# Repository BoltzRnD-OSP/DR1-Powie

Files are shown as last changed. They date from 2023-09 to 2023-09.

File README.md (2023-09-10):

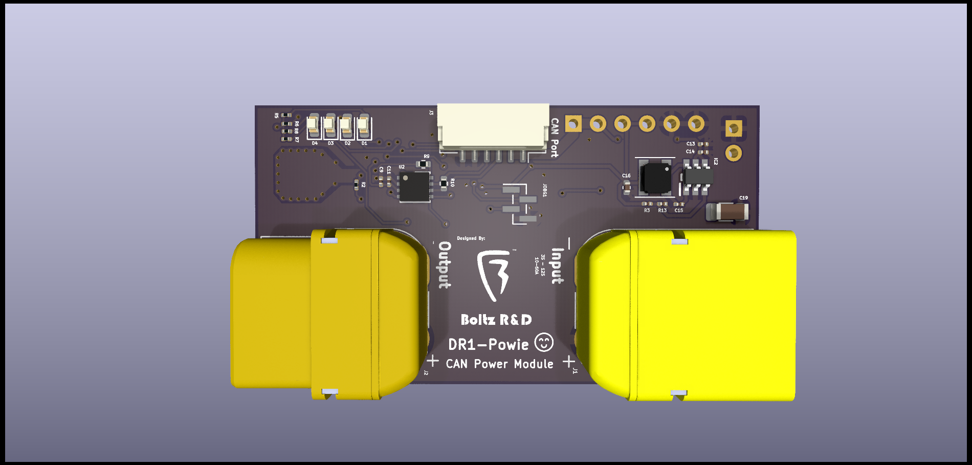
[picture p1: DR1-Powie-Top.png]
Board Top

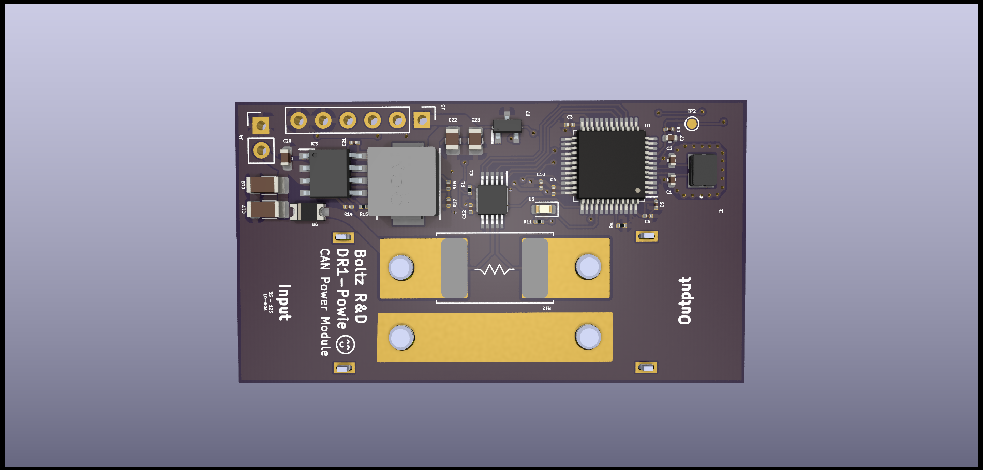
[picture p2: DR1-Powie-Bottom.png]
Board Bottom


# DR1-Powie ☺  
UAVCAN-Based Power Module for DR1 Series Flight Controllers

# Specifications:

Voltage: 3S - 12S  
Current Rating: 10A - 90A  
Embedded 5V 2A Buck to power the Flight Controller  
Battery Gauge LEDs (Will be functional in the near future)  

# License
This project is licensed under the Attribution-ShareAlike 4.0 International License.

You are free to commercially utilize the project and its derivatives. Please be generous and provide attribution! :)

THANKS!

Note: The Boltz R&D wordmark and lightning logo are trademarks of Boltz R&D. Any use other than for attribution of "this" project is strictly prohibited.

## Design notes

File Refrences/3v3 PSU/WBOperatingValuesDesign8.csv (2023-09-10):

Name | Value | Category | Description
Vout | 3.3 V | System Information | Operational Output Voltage
IC Tolerance | 20 mV | IC | IC Feedback Tolerance
Cin IRMS | 143.62 mA | Capacitor | Input capacitor RMS ripple current
Cin Pd | 83.7 µW | Capacitor | Input capacitor power dissipation
Cout IRMS | 59.6 mA | Capacitor | Output capacitor RMS ripple current
Cout Pd | 5.33 µW | Capacitor | Output capacitor power dissipation
Cinx IRMS | 8.96 mA | Capacitor | Bulk capacitor RMS ripple current
Cinx Pd | 1.61 µW | Capacitor | Bulk capacitor power dissipation
L Ipp | 206.46 mA | Inductor | Peak-to-peak inductor ripple current
L Pd | 11.23 mW | Inductor | Inductor power dissipation
Ipp percentage | 68.82% | Inductor | Inductor ripple current percentage (with respect to average inductor current)
Duty Cycle | 62.68% | System Information | Duty cycle
Efficiency | 93.5% | System Information | Steady state efficiency
Frequency | 1.1 MHz | System Information | Switching frequency
IC Tj | 34.56 °C | IC | IC junction temperature
IC Pd | 56.96 mW | IC | IC power dissipation
Pout | 990 mW | System Information | Total output power
Iin Avg | 192.44 mA | IC | Average input current
IC Ipk | 403.23 mA | IC | Peak switch current in IC
Mode | CCM | System Information | Conduction Mode
Vout p-p | 1.59 mV | System Information | Peak-to-peak output ripple voltage
Vin p-p | 39.07 mV | System Information | Peak-to-peak input voltage
Phase Marg | 62.56 ° | System Information | Bode Plot Phase Margin
Cross Freq | 25.32 kHz | System Information | Bode plot crossover frequency
Low Freq Gain | 63.92 dB | System Information | Gain at 1Hz
Gain Marg | -20.31 dB | System Information | Bode Plot Gain Margin
ICThetaJA Effective | 80 °C/W | IC | Effective IC Junction-to-Ambient Thermal Resistance
FootPrint | 77 mm² | System Information | Total Foot Print Area of BOM components
Vout Actual | 3.33 V | System Information | Vout Actual calculated based on selected voltage divider resistors
Vout Tolerance | 4.07% | System Information | Vout Tolerance based on IC Tolerance (no load) and voltage divider resistors if applicable
Vin | 5.5 V | System Information | Vin operating point
Iout | 300 mA | System Information | Iout operating point
Cin Pd | 83.7 µW | Power | Input capacitor power dissipation
Cout Pd | 5.33 µW | Power | Output capacitor power dissipation
Cinx Pd | 1.61 µW | Power | Bulk capacitor power dissipation
L Pd | 11.23 mW | Power | Inductor power dissipation
IC Pd | 56.96 mW | Power | IC power dissipation
Total BOM | $0.44 | System Information | Total BOM Cost
Total Pd | 68.4 mW | Power | Total Power Dissipation
BOM Count | 9 | System Information | Total Design BOM count

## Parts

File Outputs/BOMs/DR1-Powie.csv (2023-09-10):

Id | Designator | Footprint | Quantity | Designation | Supplier and ref
1 | C24 | C_0402_1005Metric | 1 | 100nf 100V | GRM155R62A104KE14D
2 | IC1 | SOP50P490X110-10N | 1 | INA239AIDGSR | INA239AIDGSR
3 | R12 | BVS-M-R0005-1.0 | 1 | 0.5MOhm 9W | BVS-M-R0005-1.0
4 | R19,R18 | R_0201_0603Metric | 2 | 220E 0.1% | ERA-1AEB221C
5 | D6 | D_MicroSMP_AK | 1 | V2PM10HM3/H | V2PM10HM3/H
6 | C2,C1 | C_0402_1005Metric | 2 | 8pF 1% | GCM1555C1H8R0FA16D
7 | C18,C17,C19 | C_1206_3216Metric | 3 | 4.7uF 63V | GRM31CC72A475ME11L
8 | C10,C13 | C_0201_0603Metric | 2 | 4.7uF | GRM035R60J475ME15D
9 | R14 | C_0201_0603Metric | 1 | 64.9K | RC0201FR-0764K9L
10 | IC3 | SOIC127P600X170-9N | 1 | LMR38020SDDAR | LMR38020SDDAR
11 | J5 | PinHeader_1x06_P2.54mm_Vertical | 1 | Conn_01x06 | ~
12 | TP2 | TestPoint_Pad_D1.0mm | 1 | TestPoint | ~
13 | R11,R6,R5,R7,R8 | R_0201_0603Metric | 5 | 220E | ERJ-1GNJ221C
14 | C23,C22 | C_0805_2012Metric | 2 | 47uF | GRM21BR60J476ME01K
15 | C6,C12,C3,C21,C4,C5,C14,C15 | C_0201_0603Metric | 8 | 100nf | CL03A104KQ3NNNC
16 | J4 | PinHeader_1x02_P2.54mm_Vertical | 1 | Conn_01x02 | ~
17 | R17 | C_0201_0603Metric | 1 | 10K 1% | ERJ-1GNF1002C
18 | C7 | C_0402_1005Metric | 1 | 10nf | C0402C103K4REC7411
19 | C20 | C_0603_1608Metric | 1 | 100nf 100V | CL10B104KC8NNNC
20 | R15 | R_0201_0603Metric | 1 | 100K | RC0201FR-07100KL
21 | D5,D2,D1,D4,D3 | LED_0603_1608Metric | 5 | LED | B1911USD-20D000114U1930
22 | L2 | INDPM7265X400N | 1 | 15uH 2A(Min) | SRP6540-150M
23 | R1,R4,R2 | R_0201_0603Metric | 3 | 10K | ERJ-1GNF1002C
24 | Y1 | NX3225GD8MHZSTDCRA3 | 1 | NX3225GD-8MHZ-EXS00A-CG04874 | NX3225GD-8MHZ-EXS00A-CG04874
25 | C8 | C_0201_0603Metric | 1 | 1uF | CL03A105MQ3CSNH
26 | R16 | C_0201_0603Metric | 1 | 40.2K 1% | RMCF0201FT40K2
27 | D7 | SOT95P230X117-3N | 1 | CDSOT23-T24CAN | CDSOT23-T24CAN
28 | U1 | LQFP-48_7x7mm_P0.5mm | 1 | STM32L431CBTx | STM32L431CBT6
29 | JDBG1 | PinHeader_1x04_P1.00mm_Vertical_SMD_Pin1Left | 1 | Conn_01x04 | ~
30 | C11,C9 | C_0201_0603Metric | 2 | 100nF | CL03A104KQ3NNNC
31 | R9 | R_0402_1005Metric | 1 | 10K | ERJ-1GNF1002C
32 | C16 | C_0402_1005Metric | 1 | 10uF | GRM155R60J106ME05J
33 | J2 | AMASS_XT60PW-F_1x02_P7.20mm_Horizontal | 1 | Conn_01x02 | AMASS_XT60PW-F
34 | U2 | DFN-8-1EP_3x3mm_P0.65mm_EP1.55x2.4mm | 1 | TJA1051TK-3 | TJA1051TK-3
35 | J1 | AMASS_XT60PW-M_1x02_P7.20mm_Horizontal | 1 | Conn_01x02 | AMASS_XT60PW-M
36 | R3 | C_0201_0603Metric | 1 | 69.8K | ERJ-1GNF6982C
37 | L1 | Inductor | 1 | 5.6uH 0.6A(Min) | 78438356056
38 | J3 | JST_GH_SM06B-GHS-TB_1x06-1MP_P1.25mm_Horizontal | 1 | Conn_01x06 | JST_GH_SM06B-GHS-TB
39 | R13 | C_0201_0603Metric | 1 | 22.1K | ERJ-1GNF2212C
40 | IC2 | SOT95P280X145-6N | 1 | LMR54406DBVR | LMR54406DBVR
41 | R10 | R_0402_1005Metric | 1 | 120E | CRCW0402120RJNED

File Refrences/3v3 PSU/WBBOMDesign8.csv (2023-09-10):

Part | Manufacturer | Part Number | Quantity | Price ($) | Footprint (mm²) | Description
Rfbb | Vishay-Dale | CRCW040222K1FKED | 1 | 0.01 | 3 | Resistance: 22.1 kΩ Tolerance: 1.0% Power: 63 mW
Rfbt | Vishay-Dale | CRCW040269K8FKED | 1 | 0.01 | 3 | Resistance: 69.8 kΩ Tolerance: 1.0% Power: 63 mW
Cinx | MuRata | GRM188R71H104KA93D | 1 | 0.02 | 4.68 | Cap: 100 nF Total Derated Cap: 100 nF VDC: 50 V ESR: 20 mΩ Package: 0603
L1 | NIC Components | NPI43C5R6MTRF | 1 | 0.07 | 30.74 | L: 5.6 µH DCR: 120 mΩ IDC: 1.8 A
U1 | Texas Instruments | LMR54406DBVR | 1 | 0.227 | 14.82
Cboot | MuRata | GRM155R71C104KA88D | 1 | 0.01 | 3 | Cap: 100 nF Total Derated Cap: 100 nF VDC: 16 V ESR: 1 mΩ Package: 0402
Cin | TDK | C1608X7R1A225K080AC | 1 | 0.03 | 4.68 | Cap: 2.2 µF Total Derated Cap: 1.6 µF VDC: 10 V ESR: 4.06 mΩ Package: 0603
Cout | Kemet | C0805C106K8PACTU | 2 | 0.03 | 6.75 | Cap: 10 µF Total Derated Cap: 15 µF VDC: 10 V ESR: 3 mΩ Package: 0805

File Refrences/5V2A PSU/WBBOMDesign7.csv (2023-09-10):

Part | Manufacturer | Part Number | Quantity | Price ($) | Footprint (mm²) | Description
Rfbt | Vishay-Dale | CRCW040240K2FKED | 1 | 0.01 | 3 | Resistance: 40.2 kΩ Tolerance: 1.0% Power: 63 mW
Rfbb | Vishay-Dale | CRCW040210K0FKED | 1 | 0.01 | 3 | Resistance: 10 kΩ Tolerance: 1.0% Power: 63 mW
Rpgood | Vishay-Dale | CRCW0603100KFKEA | 1 | 0.01 | 4.68 | Resistance: 100 kΩ Tolerance: 1.0% Power: 100 mW
Cboot | MuRata | GRM155R71C104KA88D | 1 | 0.01 | 3 | Cap: 100 nF Total Derated Cap: 100 nF VDC: 16 V ESR: 1 mΩ Package: 0402
Cinx | TDK | C2012X7R2A104K125AA | 1 | 0.03 | 6.75 | Cap: 100 nF Total Derated Cap: 100 nF VDC: 100 V ESR: 20.73 mΩ Package: 0805
Rt | Vishay-Dale | CRCW060364K9FKEA | 1 | 0.01 | 4.68 | Resistance: 64.9 kΩ Tolerance: 1.0% Power: 100 mW
L1 | NIC Components | NPI52W150MTRF | 1 | 0.264 | 358.11 | L: 15 µH DCR: 36 mΩ IDC: 4 A
Cout | MuRata | GRM32ER61C476KE15L | 2 | 0.17 | 14.7 | Cap: 47 µF Total Derated Cap: 63 µF VDC: 16 V ESR: 3.04 mΩ Package: 1210
Cin | TDK | C3225X7S2A475M200AB | 3 | 0.45 | 14.7 | Cap: 4.7 µF Total Derated Cap: 3.6 µF VDC: 100 V ESR: 5.89 mΩ Package: 1210
U1 | Texas Instruments | LMR38020FDDAR | 1 | 0.596 | 55.2

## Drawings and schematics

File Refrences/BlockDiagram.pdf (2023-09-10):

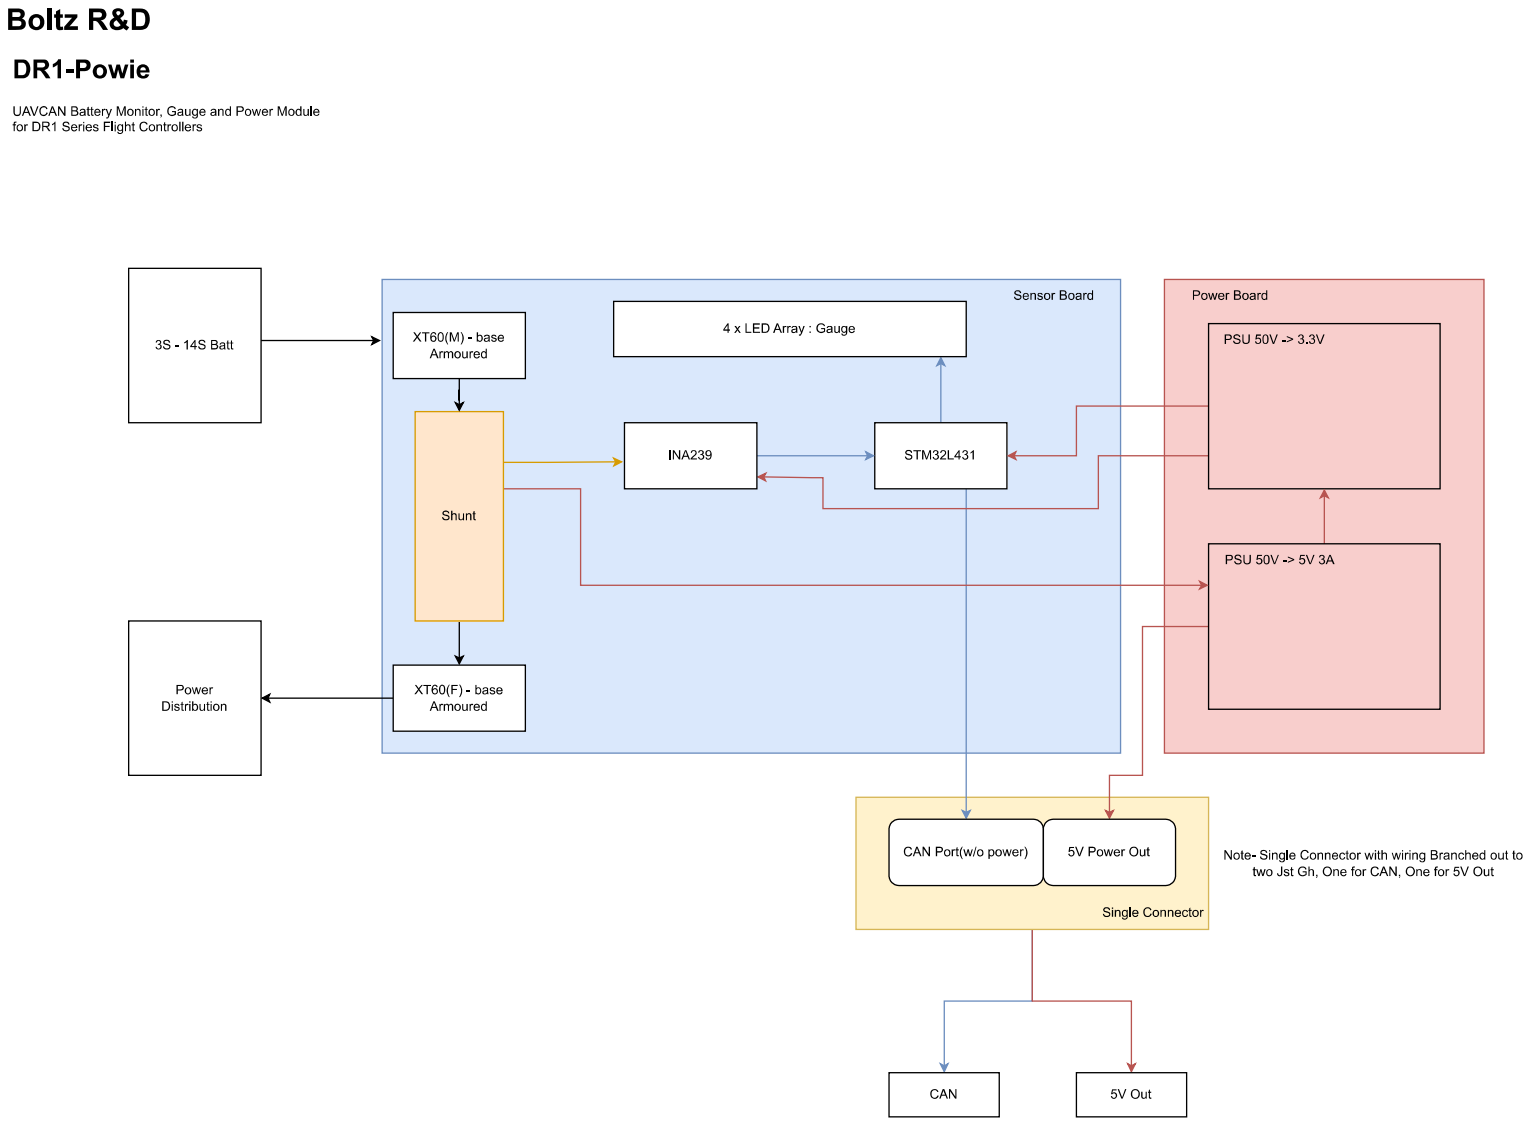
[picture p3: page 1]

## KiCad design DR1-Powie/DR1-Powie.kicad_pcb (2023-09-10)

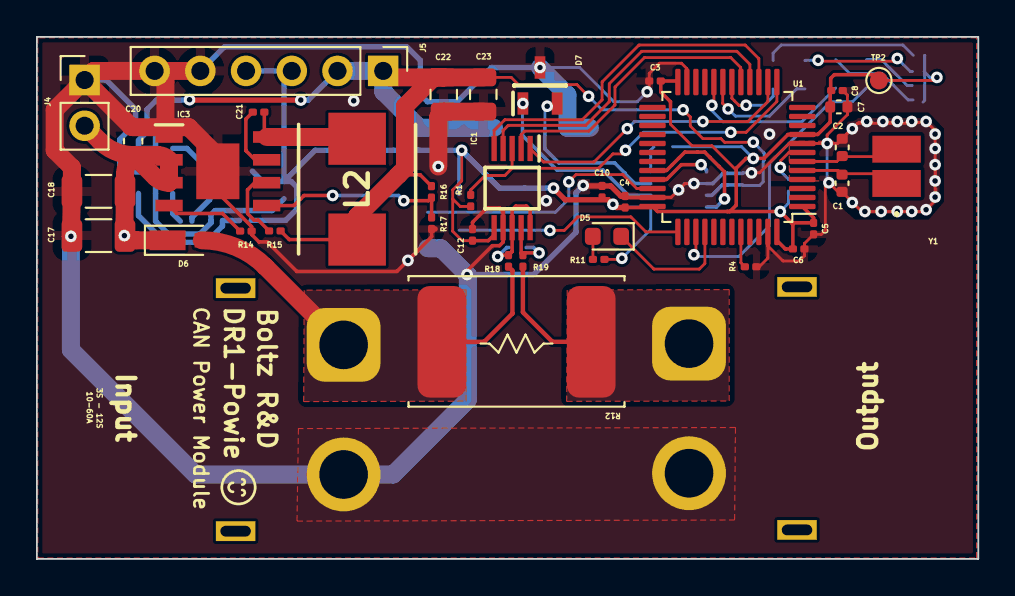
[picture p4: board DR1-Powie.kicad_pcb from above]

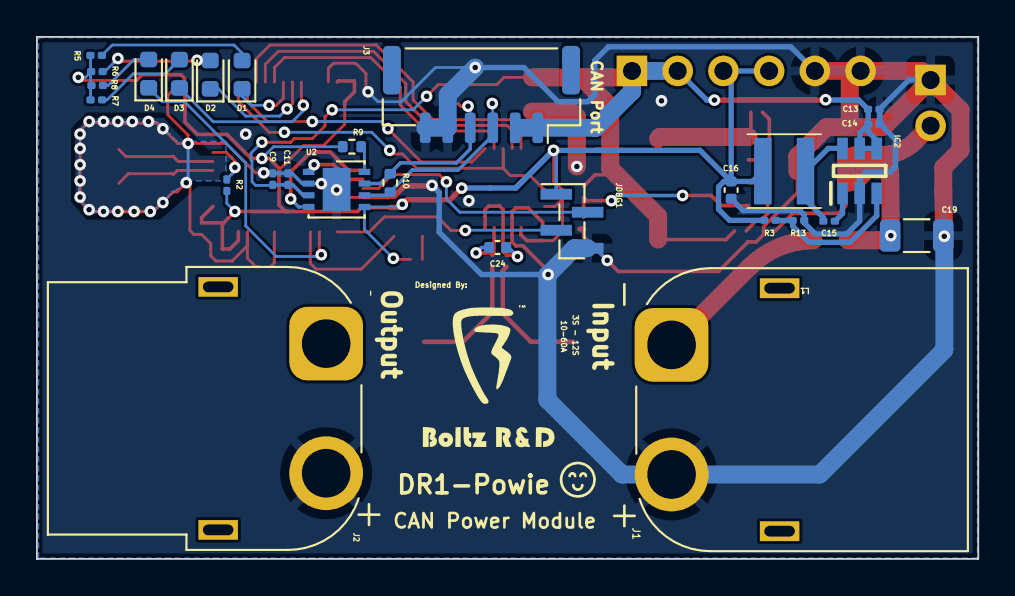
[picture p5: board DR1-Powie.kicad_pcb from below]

Board: 2 copper layers, 52.3 x 29.0 mm, 65 parts (28 on the bottom side), 42 nets.

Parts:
C1, C2: 8pF 1%; C_0402_1005Metric
C3, C4, C5, C6, C12, C14, C15, C21: 100nf; C_0201_0603Metric
C7: 10nf; C_0402_1005Metric
C8: 1uF; C_0201_0603Metric
C9, C11: 100nF; C_0201_0603Metric
C10, C13: 4.7uF; C_0201_0603Metric
C16: 10uF; C_0402_1005Metric
C17, C18, C19: 4.7uF 63V; C_1206_3216Metric
C20: 100nf 100V; C_0603_1608Metric
C22, C23: 47uF; C_0805_2012Metric
C24: 100nf 100V; C_0402_1005Metric
D1, D2, D3, D4, D5: LED; LED_0603_1608Metric
D6: V2PM10HM3/H; D_MicroSMP_AK
D7: CDSOT23-T24CAN; SOT95P230X117-3N
IC1: INA239AIDGSR; SOP50P490X110-10N
IC2: LMR54406DBVR; SOT95P280X145-6N
IC3: LMR38020SDDAR; SOIC127P600X170-9N
J1: Conn_01x02; AMASS_XT60PW-M_1x02_P7.20mm_Horizontal
J2: Conn_01x02; AMASS_XT60PW-F_1x02_P7.20mm_Horizontal
J3: Conn_01x06; JST_GH_SM06B-GHS-TB_1x06-1MP_P1.25mm_Horizontal
J4: Conn_01x02; PinHeader_1x02_P2.54mm_Vertical
J5: Conn_01x06; PinHeader_1x06_P2.54mm_Vertical
JDBG1: Conn_01x04; PinHeader_1x04_P1.00mm_Vertical_SMD_Pin1Left
L1: 5.6uH 0.6A(Min); Inductor
L2: 15uH 2A(Min); INDPM7265X400N
R1, R2, R4: 10K; R_0201_0603Metric
R3: 69.8K; C_0201_0603Metric
R5, R6, R7, R8, R11: 220E; R_0201_0603Metric
R9: 10K; R_0402_1005Metric
R10: 120E; R_0402_1005Metric
R12: 0.5MOhm 9W; BVS-M-R0005-1.0
R13: 22.1K; C_0201_0603Metric
R14: 64.9K; C_0201_0603Metric
R15: 100K; R_0201_0603Metric
R16: 40.2K 1%; C_0201_0603Metric
R17: 10K 1%; C_0201_0603Metric
R18, R19: 220E 0.1%; R_0201_0603Metric
TP2: TestPoint; TestPoint_Pad_D1.0mm
U1: STM32L431CBTx; LQFP-48_7x7mm_P0.5mm
U2: TJA1051TK-3; DFN-8-1EP_3x3mm_P0.65mm_EP1.55x2.4mm
Y1: NX3225GD-8MHZ-EXS00A-CG04874; NX3225GD8MHZSTDCRA3

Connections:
+5V: C9.1, C11.1, C13.1, C14.1, C22.1, C23.1, IC2.4 (EN), IC2.5 (VIN), J3.1, J3.2, J5.1, J5.2, L2.2, R15.1, R16.1, U2.3 (VCC)
+BATT: C17.1, C18.1, C19.1, C20.1, D6.1 (K), IC3.2 (EN), IC3.3 (VIN), J4.2
BOOT0: R4.1, U1.44 (PH3)
CAN1_RX: U1.32 (PA11), U2.4 (RXD)
CAN1_TX: U1.33 (PA12), U2.1 (TXD)
CAN_H_1: D7.2 (K2), J3.4, R10.1, U2.7 (CANH)
CAN_L_1: D7.1 (K1), J3.3, R10.2, U2.6 (CANL)
CSENSE1: C24.1, IC1.8 (VBUS), IC1.10 (IN+), R18.1
CSENSE2: C24.2, IC1.9 (IN-), R19.1
CSNSR_ALERT: IC1.3 (ALERT), R1.1, U1.13 (PA3)
CSNSR_CS: IC1.1 (CS), U1.14 (PA4)
CSNSR_MISO: IC1.4 (MISO), U1.16 (PA6)
CSNSR_MOSI: IC1.2 (MOSI), U1.17 (PA7)
CSNSR_SCLK: IC1.5 (SCLK), U1.15 (PA5)
FMU_SWCLK: JDBG1.3, U1.37 (PA14)
FMU_SWDIO: JDBG1.2, U1.34 (PA13)
GAUGE_LED1: D1.1 (K), U1.18 (PB0)
GAUGE_LED2: D2.1 (K), U1.19 (PB1)
GAUGE_LED3: D3.1 (K), U1.20 (PB2)
GAUGE_LED4: D4.1 (K), U1.39 (PB3)
GND: C1.2, C2.2, C3.2, C4.2, C5.2, C6.2, C7.2, C8.2, C9.2, C10.2, C11.2, C12.2, C13.2, C14.2, C16.2, C17.2, C18.2, C19.2, C20.2, C22.2, C23.2, D7.3 (K3), IC1.7 (GND), IC2.2 (GND), IC3.1 (GND), IC3.9 (EP), J1.2, J2.2, J3.5, J3.6, J4.1, J5.5, J5.6, JDBG1.4, R4.2, R13.2, R14.2, R17.2, U1.8 (VSSA), U1.23 (VSS), U1.35 (VSS), U1.47 (VSS), U2.2 (GND), U2.9 (GND)
MCU_OSCIN: C1.1, U1.5 (PH0), Y1.1
MCU_OSCOUT: C2.1, U1.6 (PH1), Y1.2
unnamed: D1.2 (A), R5.1
unnamed: D2.2 (A), R6.1
unnamed: D3.2 (A), R7.1
unnamed: D4.2 (A), R8.1
unnamed: D5.2 (A), R11.1
unnamed: C15.2, IC2.1 (CB)
unnamed: IC2.3 (FB), R3.2, R13.1
unnamed: C15.1, IC2.6 (SW), L1.1
unnamed: C21.1, IC3.7 (BOOT)
unnamed: IC3.5 (FB), R16.2, R17.1
unnamed: IC3.6 (PG), R15.2
unnamed: IC3.4 (RT/SYNC), R14.1
unnamed: C21.2, IC3.8 (SW), L2.1
unnamed: R2.1, U1.7 (NRST)
unnamed: R9.1, U2.8 (S)
PSU: D6.2 (A), J1.1, R12.2, R18.2
PSU2: J2.1, R12.1, R19.2
UI_LED: D5.1 (K), U1.40 (PB4)
VDD: C3.1, C4.1, C5.1, C6.1, C7.1, C8.1, C10.1, C12.1, C16.1, IC1.6 (VS), J5.3, J5.4, JDBG1.1, L1.2, R1.2, R2.2, R3.1, R5.2, R6.2, R7.2, R8.2, R9.2, R11.2, TP2.1, U1.1 (VBAT), U1.9 (VDDA), U1.24 (VDD), U1.36 (VDD), U1.48 (VDD), U2.5 (VIO)
